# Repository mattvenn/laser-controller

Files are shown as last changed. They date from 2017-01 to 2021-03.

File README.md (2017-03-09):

# Epilog 32 ex usage & control system

## Control System

* internet connection to download current valid RFID cards
* enable laser with valid RFID card
* post usage to net every minute
* disable laser after X seconds without laser being used

### Electronics

* ESP8266
* 2 channel relay & driver
* RFID reader
* ws2812 RGB status light

* [photo of pcb](https://goo.gl/photos/raj6Eu2eDnTMet147)
* [pdf schematic](control-board/schematic.pdf)

#### Problems & Fixes

* Sometimes rfid reader seems to get blocked
* Sometimes laser pulse isn't detected so laser is switched off - fixed by
 Guillem, was an interrupt issue
* Sometimes relay turns on but laser won't fire - fixed with new pcb (breadboard
 bad ground connections)
 
### Software

* ESP8266 checks RFID against remote DB
* if valid, light LED
* turn on relay to connect DSUB25 lines 7&8.
* laser DSUB25 pin 7 -> interrupt on pin 14,
* while interrupt is firing post usage to phant

[esp8266 firmware](firmware/src/)

[Dashboard](http://freeboard.cursivedata.co.uk/index.html?load=dust.json)

[Logs](http://phant.cursivedata.co.uk/streams/kBd098lqXzu3mYJOX9YYckorrEy)

## Control reverse engineering

Neither Epilog or Coherent were willing to share the DSUB 25 pinout that controls the Coherent C Series laser model 1138402-AA.

Searching for the DSUB 25 format, only references to [ILDA](https://www.laserworld.com/en/show-laser-light-faq/technical-show-laser-faq/laser-projectors-technical-faq/1140-how-is-the-ilda-connector-pinout.html) were found.

A [board](bob/) that connects straight through 2 x DSUB 25 was designed in Kicad and milled

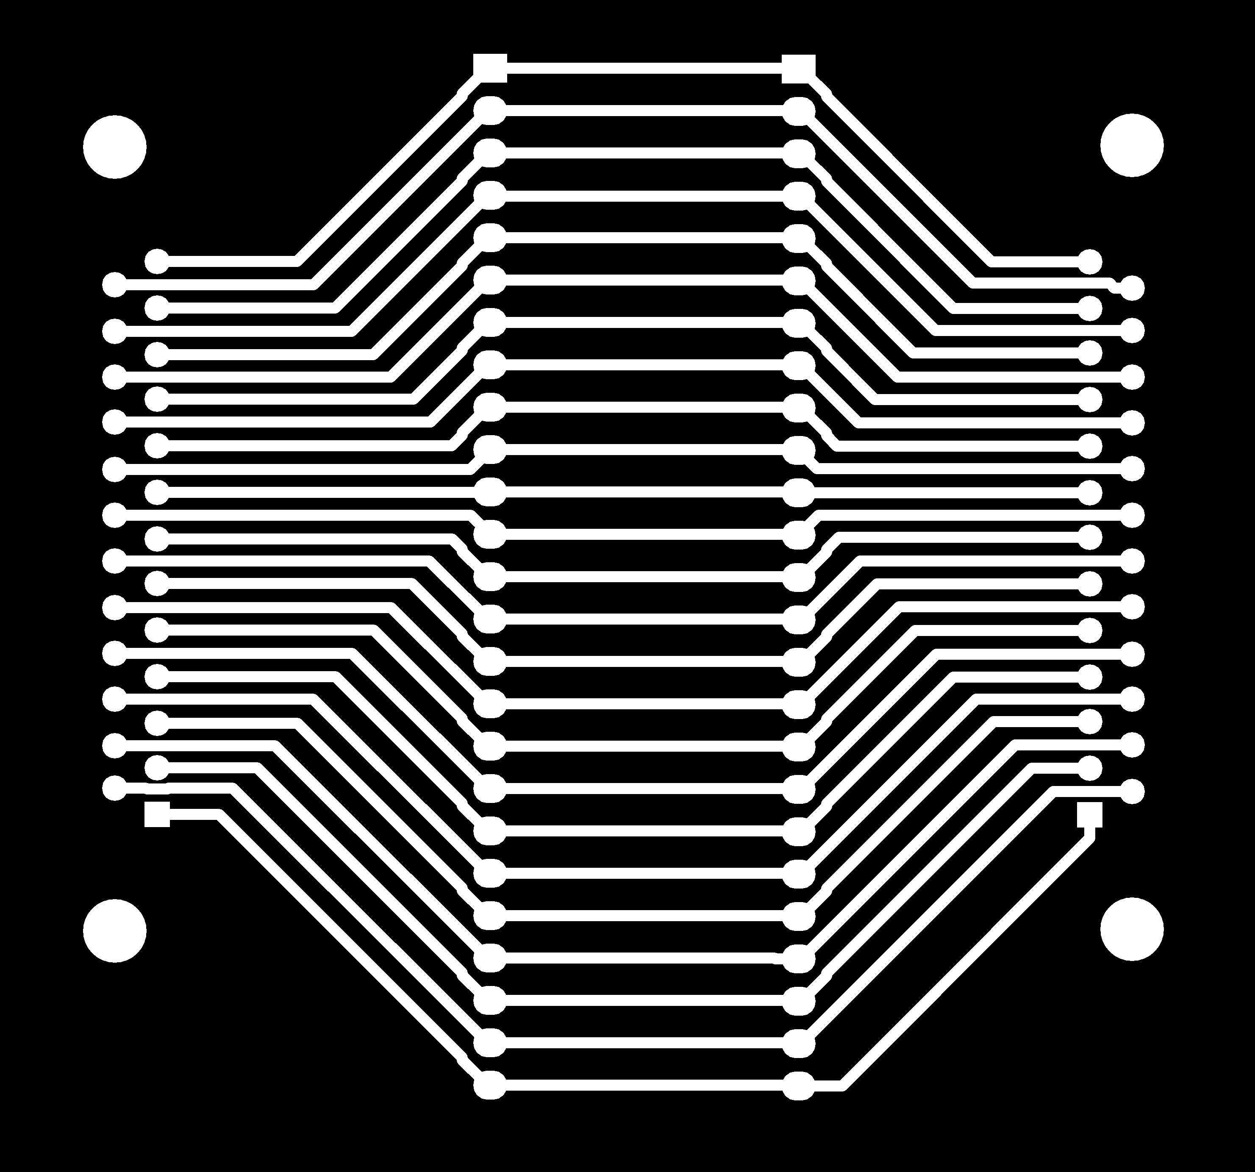
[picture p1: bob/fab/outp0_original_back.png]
board back


After finding system ground, all pins were tested with laser on and off:

| Pin | Laser On | Laser Off | 
| --- | --- | --- |
|1|0|0
|2|0|0
|3|5|5
|4|0|0
|5|0|0
|6|5|5
|7|5->0|0
|8|5|5
|9|5|5
|10|5|5
|11|5|5
|12|5|5
|13|0|0
|14|5|5
|15|5|5
|16|GND|GND
|17|0|0
|18|0|0
|19|0|0
|20|0->5|5
|21|0|0
|22|5|5
|23|5|5
|24|5|5
|25|15|15

Only pins 7 & 20 seemed to have any change when lasing. Also thought that they would be a differential signal.
Cracking out the scope gave these results for rastering, lasing at 50% power and 100% power.

Scope channel 1 is pin 7, channel 2 is 20.

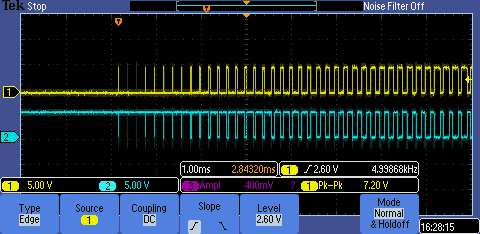
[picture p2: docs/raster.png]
raster


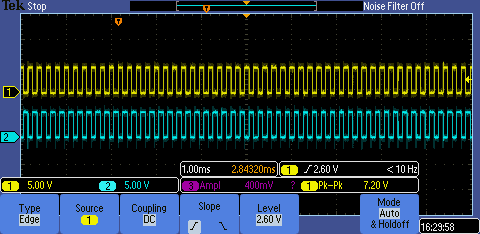
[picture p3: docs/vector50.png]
50%


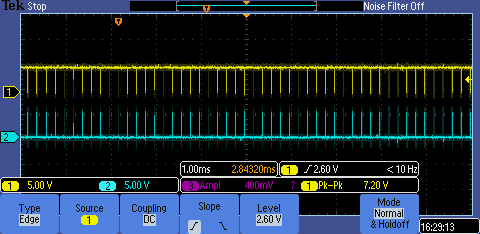
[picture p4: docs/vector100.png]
100%


Breaking connection to either pin 7 or 20 made no difference, only breaking both lines stopped the laser.

Also tested was breaking pin 4 as ILDA showed that as being the interlock signal, it made no difference.

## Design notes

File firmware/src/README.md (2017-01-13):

## Secrets

fill in the blanks of not_secret.h and then rename to secrets.h

## Dependencies

* git@github.com:miguelbalboa/rfid.git

## SPI RFID reader

[spi details](http://d.av.id.au/blog/esp8266-hardware-spi-hspi-general-info-and-pinout/)

* SPI SS_PIN 15
* SPI MOSI 13
* SPI MISO 12
* SPI CLK 14
* RST_PIN 5
* LED 4

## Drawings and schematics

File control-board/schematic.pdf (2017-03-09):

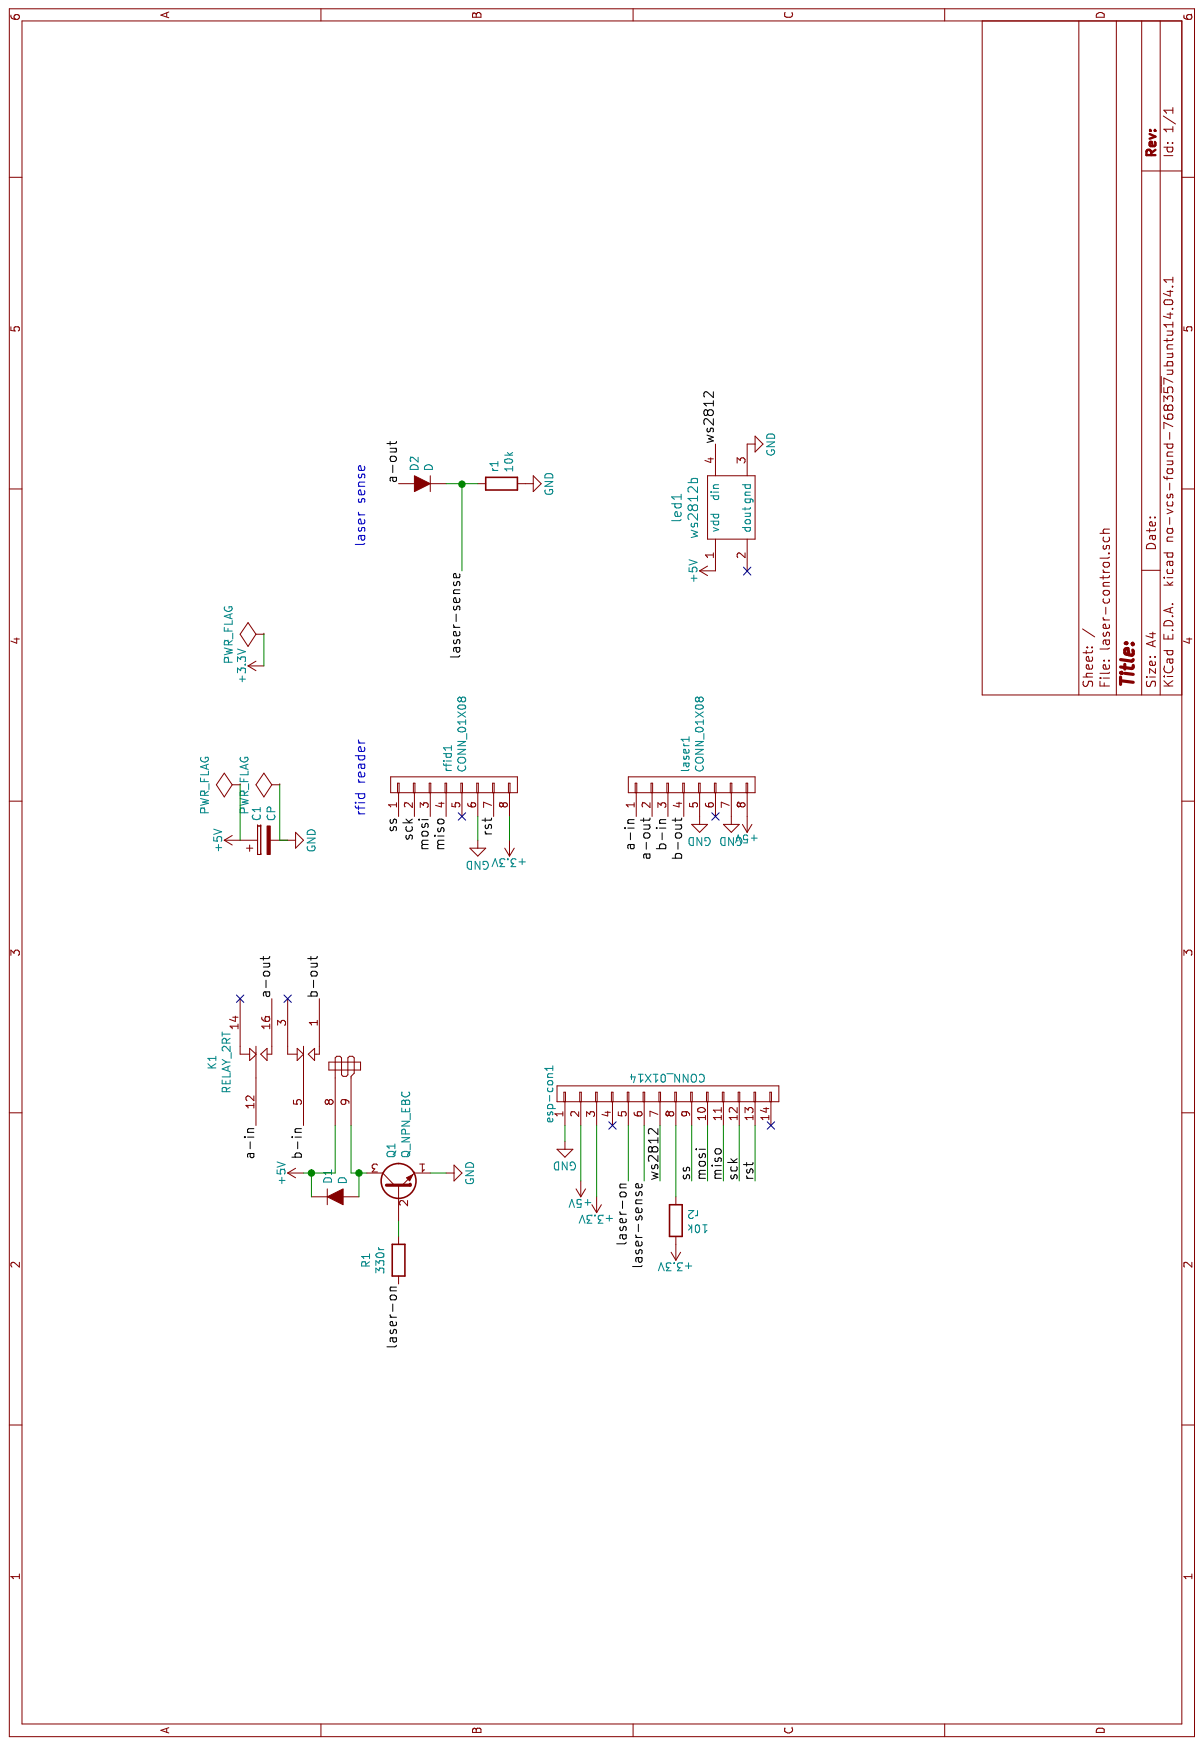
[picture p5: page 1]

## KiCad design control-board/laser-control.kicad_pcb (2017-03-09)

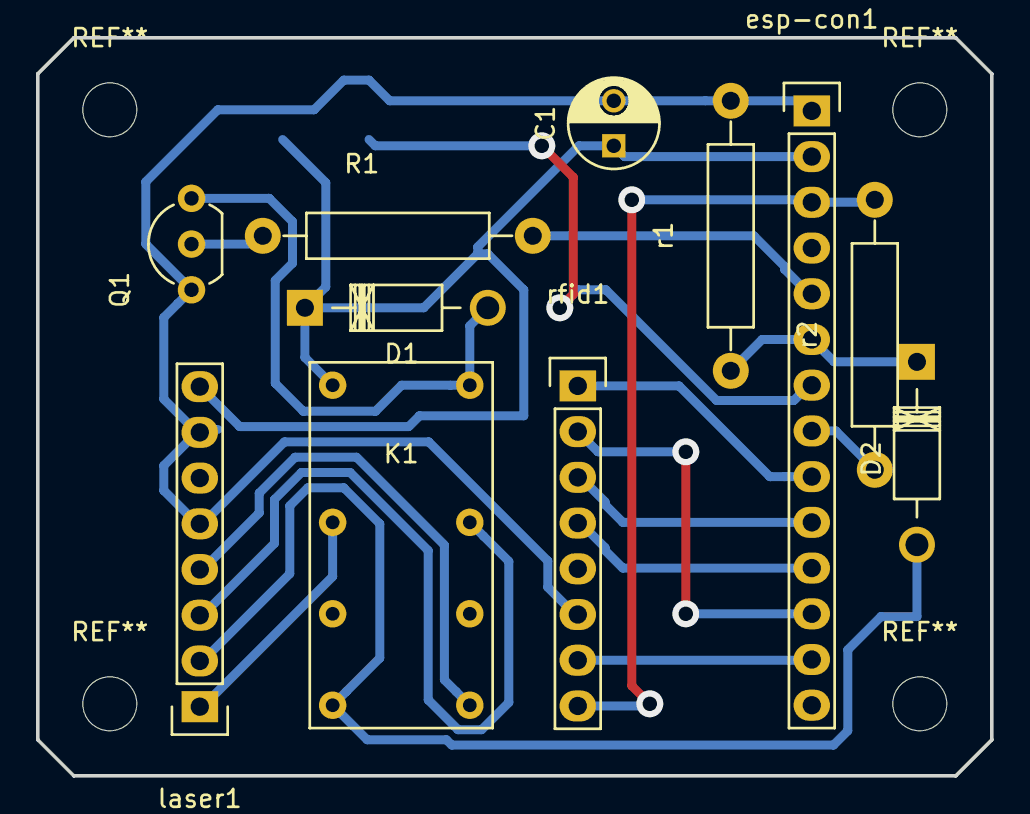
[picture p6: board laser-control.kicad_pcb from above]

Board: 2 copper layers, 53.0 x 41.0 mm, 12 parts (1 on the bottom side), 18 nets.

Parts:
C1: CP; C_Radial_D5_L6_P2.5
D1, D2: D; Diode_DO-41_SOD81_Horizontal_RM10
K1: RELAY_2RT; relay
Q1: Q_NPN_EBC; TO-92_Inline_Wide
R1: 330r; Resistor_Horizontal_RM15mm
esp-con1: CONN_01X14; Pin_Header_Straight_1x14
laser1: CONN_01X08; Pin_Header_Straight_1x08
led1: ws2812b; WS2812B
r1, r2: 10k; Resistor_Horizontal_RM15mm
rfid1: CONN_01X08; Pin_Header_Straight_1x08

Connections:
+3V3: esp-con1.3, r2.2, rfid1.8
+5V: C1.1, D1.1, K1.8, esp-con1.2, laser1.8, led1.1
/a-in: K1.12, laser1.1
/a-out: D2.2, K1.16, laser1.2
/b-in: K1.5, laser1.3
/b-out: K1.1, laser1.4
/laser-on: R1.2, esp-con1.5
/laser-sense: D2.1, esp-con1.6, r1.1
/miso: esp-con1.11, rfid1.4
/mosi: esp-con1.10, rfid1.3
/rst: esp-con1.13, rfid1.7
/sck: esp-con1.12, rfid1.2
/ss: esp-con1.9, rfid1.1
/ws2812: esp-con1.7, led1.4
GND: C1.2, Q1.1, esp-con1.1, laser1.5, laser1.7, led1.3, r1.2, rfid1.6
unnamed: D1.2, K1.9, Q1.3
unnamed: Q1.2, R1.1
unnamed: esp-con1.8, r2.1

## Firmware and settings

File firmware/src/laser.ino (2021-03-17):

#include <pgmspace.h>
#include <ESP8266WiFi.h>
#include "secrets.h"
#include <NeoPixelBus.h>

const uint16_t PixelCount = 1; 
const uint8_t PixelPin = 0;

#define colorSaturation 255

// three element pixels, in different order and speeds
NeoPixelBus<NeoGrbFeature, NeoEsp8266BitBang800KbpsMethod> strip(PixelCount, PixelPin);

#define LASER_IN 4 // has an external 10k pull down and diode for protection of laser in/outs
#define RELAY 5 // also wired to an LED
#define LASER_ON_LED 2
/*
SPI MOSI 13
SPI MISO 12
SPI CLK 14
*/
#define SS_PIN 15
#define RST_PIN 16

#define POST_TIME_MS 60000 // how often log is posted
#define LASER_OFF_DELAY_MS 30000 // how long after the last control pulse do we assume laser is finished
#define AUTH_TIMEOUT_MS 60000 // how long till rfid current card times out
#define MAX_CONNECT_ATTEMPTS 10

// eeprom addresses (storing 2byte ints so each address is +2)
#define EEP_WIFI_CONN 0
#define EEP_REBOOTS 2 

// state machine defs
#define AUTH_START 1
#define AUTH_WAIT_RFID 2
#define AUTH_WAIT_LASER 3

#define LOG_START 1
#define LOG_WAIT 2
#define LOG_POSTING 3

#define MAX_USERS 10 

struct CARD {
    String name;
    String rfid;
    } users [MAX_USERS];


int num_users = 0;
int auth_state = AUTH_START; // 2 differnt state machines: auth and log
int log_state = LOG_START;

RgbColor red(colorSaturation, 0, 0);
RgbColor green(0, colorSaturation, 0);
RgbColor blue(0, 0, colorSaturation);

void setup()
{
    Serial.begin(9600);
    Serial.println();
    Serial.println();
    strip.Begin();

    // update number of times rebooted
    setupEEPROM();
    EEPROMWriteInt(EEP_REBOOTS, EEPROMReadInt(EEP_REBOOTS) + 1);
    /*
    EEPROMWriteInt(EEP_REBOOTS, 0);
    EEPROMWriteInt(EEP_WIFI_CONN, 0);
    */

    // pin modes
    pinMode(LASER_IN, INPUT);
    digitalWrite(LASER_IN, false);
    pinMode(LASER_ON_LED, OUTPUT);
    pinMode(RELAY, OUTPUT);
    digitalWrite(RELAY, false);
    digitalWrite(LASER_ON_LED, false);

    setup_rfid();

}

volatile unsigned long last_on = 0;
boolean laser_on = false;
String current_rfid = "";

ICACHE_RAM_ATTR void laser_ISR()
{
    last_on = millis();
}

void loop()
{
    static unsigned long start_time;
    static unsigned long auth_time;
    delay(100);
    strip.Show();

    switch(auth_state)
    {
        case AUTH_START:
        {
            // laser starts off
            strip.SetPixelColor(0, red);
            Serial.println("auth start");
            digitalWrite(RELAY, false);
            auth_state = AUTH_WAIT_RFID;
            // think interrupts interfere with the rfid reader
            detachInterrupt(digitalPinToInterrupt(LASER_IN)); 
            break;
        }
        case AUTH_WAIT_RFID:
        {
            Serial.println("rfid wait");
            current_rfid = read_rfid();
            // rfid is present
            if(current_rfid != "")
            {
                Serial.println(current_rfid);
                if(valid_rfid(current_rfid))
                {
                    Serial.println("ok");
                    // turn on relay to enable laser
                    digitalWrite(RELAY, true);
                    auth_state = AUTH_WAIT_LASER;
                    auth_time = millis();

                    // attach laser interrupt
                    attachInterrupt(digitalPinToInterrupt(LASER_IN), laser_ISR, RISING); 
                    strip.SetPixelColor(0, green);
                }
                else
                {
                    Serial.println("bad id");
                }
            }
            // no rfid present
            break;
        }
        case AUTH_WAIT_LASER:
        {
            Serial.print("WAIT LASER: ");
            /*
            Work out if the laser is on or off. The interrupt fires on positive edges
            of the pulses that are used to control the laser.

            - only valid after first interrupt occurs
            - even if long posting time, the result of this will
              be valid because interrupts stay enabled while posting
            */
            cli(); // disable interrupts
            if(last_on != 0)
                laser_on = millis() - last_on < LASER_OFF_DELAY_MS ? true : false;

            Serial.print(millis() - last_on);
            Serial.print(",");
            Serial.println(laser_on);

            sei(); // enable interrupts

            if(laser_on)
            {
                strip.SetPixelColor(0, blue);
            }
            else
            {
                strip.SetPixelColor(0, green);
            }

            // turn off laser if it is not firing
            if(laser_on == false && (millis() - auth_time > AUTH_TIMEOUT_MS))
            {
                Serial.println("laser off, going to auth start");
                auth_state = AUTH_START;
            }
            break;
        }
    }

    //log state machine
    switch(log_state)
    {
        case LOG_START:
        {
            // start wifi if necessary 
            if(WiFi.status() != WL_CONNECTED) 
                start_wifi();

            // fetch users, 1st request after initial connect always fails - so repeat ;(
            if(num_users == 0)
                fetch_users();
            if(num_users == 0)
                fetch_users();

            start_time = millis();
            log_state = LOG_WAIT;
            break;
        }
        case LOG_WAIT:
        {
            if((millis() - start_time) > POST_TIME_MS)
                log_state = LOG_POSTING;
            break;
        }
        case LOG_POSTING:
        {
            Serial.println("posting");
            post(laser_on, current_rfid);
            log_state = LOG_START;
            break;
        }
    }
}

void fetch_users()
{
    WiFiClient client;
    const int httpPort = 80;

    Serial.print("connecting to ");
    Serial.println(user_host);

    if(!client.connect(user_host, httpPort)) 
    {
        Serial.println("failed to fetch users");
        return;
    }

    String url = "/files/users.csv";
    Serial.print("Requesting users from : ");
    Serial.println(url);
    delay(100);

    // This will send the request to the server
    client.print(String("GET ") + url + " HTTP/1.1\r\n" +
                 "Host: " + user_host + "\r\n" + 
                 "Connection: close\r\n\r\n");

    int timeout = 0;
    while(!client.available())
    {
        Serial.print(".");
        if(timeout ++ > 10)
            break;;
        delay(100);
    }
    
    // Read all the lines of the reply from server and print them to Serial
    boolean csv_start = false;
    while(client.available() && num_users < MAX_USERS)
    {
        String line = client.readStringUntil('\n');
        Serial.println(line);
        if(csv_start)
        {
            int comma = line.indexOf(',');
            if(comma)
            {
                users[num_users].name = line.substring(0, comma);
                users[num_users].rfid = line.substring(comma+1);
                Serial.print(num_users);
                Serial.print(" : ");
                Serial.print(users[num_users].name);
                Serial.print(" = ");
                Serial.println(users[num_users].rfid);
                num_users ++;
            }
        }
        if(line.charAt(0) == '\r')
            csv_start = true;
    }
  
    Serial.print("fetched: ");
    Serial.println(num_users);
}

// todo - make request to mattvenn.net with rfid and check it's OK
bool valid_rfid(String rfid)
{
    for(int i=0; i<num_users; i++)
    {
        if(users[i].rfid == rfid)
        {
            Serial.println(users[i].name);
            return true;
        }
    }
    return false;
}

void post(boolean laser_on, String current_rfid)
{
    //send the data to sparkfun
    Serial.print("connecting to ");
    Serial.println(host);
    
    // Use WiFiClient class to create TCP connections
    WiFiClient client;
    const int httpPort = 80;
    if(!client.connect(host, httpPort)) 
    {
        Serial.println("connection failed");
        return;
    }
    
    // We now create a URI for the request
    String url = "/input/";
    url += streamId;
    url += "?private_key=";
    url += privateKey;
    url += "&laser=";
    url += laser_on;
    url += "&rfid=";
    url += current_rfid;
    url += "&uptime=";
    url += millis();
    url += "&num_boots=";
    url += EEPROMReadInt(EEP_REBOOTS);
    url += "&num_connects=";
    url += EEPROMReadInt(EEP_WIFI_CONN);
    
    Serial.print("Requesting URL: ");
    Serial.println(url);

    // This will send the request to the server
    client.print(String("GET ") + url + " HTTP/1.1\r\n" +
                 "Host: " + host + "\r\n" + 
                 "Connection: close\r\n\r\n");
    delay(10);
    
    // Read all the lines of the reply from server and print them to Serial
    while(client.available())
    {
        String line = client.readStringUntil('\r');
        Serial.print(line);
    }
  
    Serial.println();
    Serial.println("closing connection");
}

void start_wifi()
{
    Serial.print("Connecting to ");
    Serial.println(ssid);

    WiFi.begin(ssid, password);

    int count = 0;
    while (WiFi.status() != WL_CONNECTED) 
    {
        delay(500);
        Serial.print(".");
        // don't hang if no internet
        if(count > MAX_CONNECT_ATTEMPTS)
            break;
    }
    Serial.println("");
    EEPROMWriteInt(EEP_WIFI_CONN, EEPROMReadInt(EEP_WIFI_CONN) + 1);
    
    if(WiFi.status() == WL_CONNECTED)
    {
        Serial.println("WiFi connected");  
        Serial.println("IP address: ");
        Serial.println(WiFi.localIP());
    }

    delay(1000);
}

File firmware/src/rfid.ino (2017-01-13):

#include <SPI.h>
#include <MFRC522.h>

MFRC522 mfrc522(SS_PIN, RST_PIN);	// Create MFRC522 instance

void setup_rfid()
{
    SPI.begin();			// Init SPI bus
    mfrc522.PCD_Init();		// Init MFRC522
}

String read_rfid()
{
    String rfid = "";
    byte bufferATQA[2];
	byte bufferSize = sizeof(bufferATQA);
	byte result = mfrc522.PICC_WakeupA(bufferATQA, &bufferSize);
	if(result != mfrc522.STATUS_OK)
        return rfid;
	// Look for new cards
	//if ( ! mfrc522.PICC_IsNewCardPresent()) {
	//	return rfid;
//	}
	// Select one of the cards
	if ( ! mfrc522.PICC_ReadCardSerial()) {
		return rfid;
	}
	
        mfrc522.PICC_HaltA();
	for (byte i = 0; i < mfrc522.uid.size; i++) 
	{
		if(mfrc522.uid.uidByte[i] < 0x10)
		rfid.concat("0");
		rfid.concat(String(mfrc522.uid.uidByte[i], HEX));
	} 

	return rfid;
}

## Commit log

2017-01-12 net & schematic
    [laser25.sch]
2017-01-13 after validating rfid, dont turn off laser if net is down
2017-01-25 add users and increases laser time delay
2017-01-30 External diode protection
2017-02-02 disable interrupts while waiting for rfid
2017-02-03 move laser detection to auth state machine, tidy up and increased timeouts
2017-02-16 get users from csv
    [users.csv]
2017-02-22 disable interrupts while checking time
2017-03-09 laser control board
    [laser-control.kicad_pcb, laser-control.sch]
2017-03-09 pdf schematic
2017-03-09 notes on pcb
2017-04-03 added Luis
    [users.csv]
